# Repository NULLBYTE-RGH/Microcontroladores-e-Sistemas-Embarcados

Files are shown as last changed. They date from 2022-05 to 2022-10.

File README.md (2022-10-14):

Microcontroladores-e-Sistemas-Embarcados

# Projeto Fechadura Smart:

## Microcontrolador: raspberry pi pico

## Lista de componentes:

- Leitor de Digital DY50
- Teclado Matricial 4x4
- Solenoid 12v 0,9 A
- Display OLed SPI 128 X 32
- RFID MFRC-522
- Acelerometro MPU 6050
- Buzzer
- ESP 8266

## Placa e componentes Basicos:

- Placa de fenolite 10 x 20 Cm 
- Transistor TIP-310
- Reguladores [LM1117, L7805] 12 v -> 6 v e 6 v -> 3.3
- Resistores [300 Ω, 2.2k Ω] 300 Ω controle base do Transistor e 2.2k Ω PULL-UP na entrada RX do leitor de Digital
- 3 Capacitores 100 µF para remoção de ruído das entradas e saidas dos reguladores

## FrontEnd:

- React
- Bootstrap
- Fontawesome

- [x] O Servidor de aplicação sera um Raspberry Pi 3, o qual ira se comunicar com a fechadura por meio de WIFI com um AP gerado pelo ESP-8266 que ficara junto com a fechadura.
- [x] A comunicação se dara por meio de uma API REST.

### Trilhas

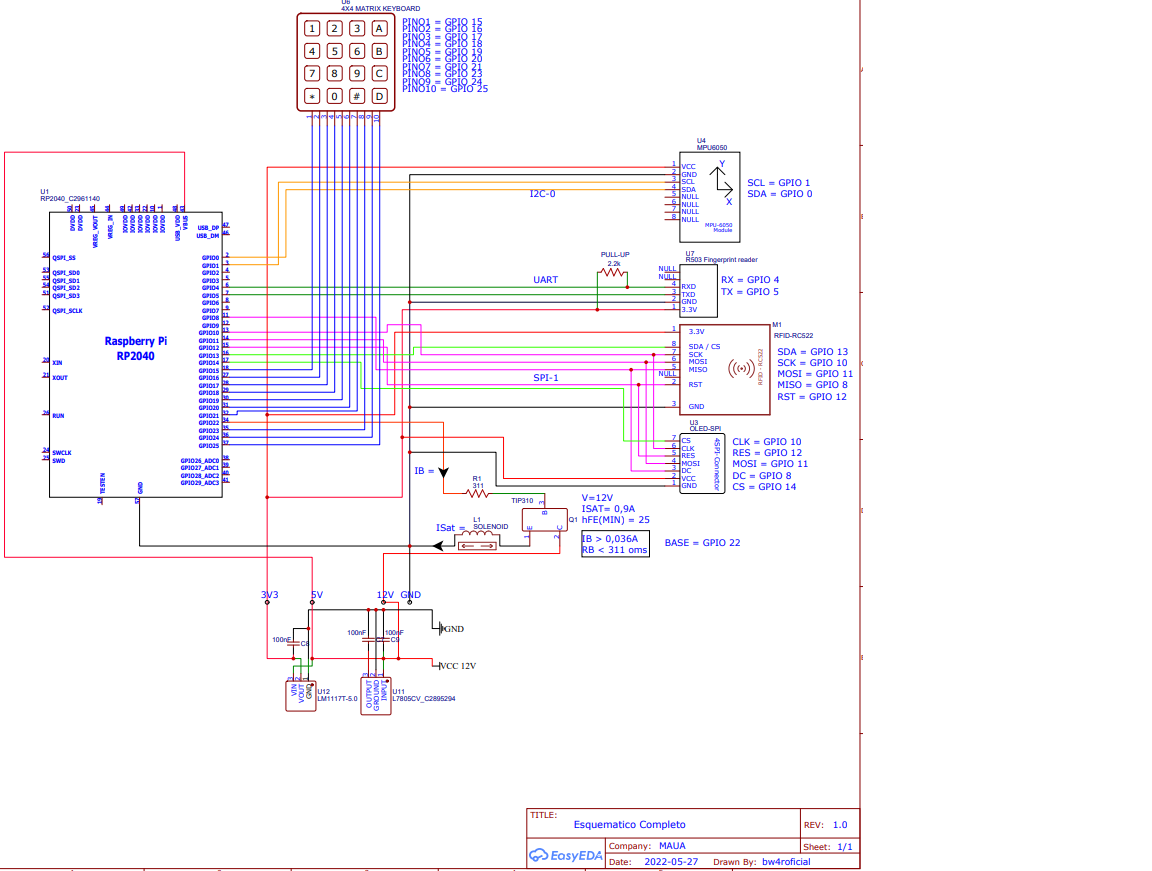
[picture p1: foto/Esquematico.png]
EsquemaDeTrilhas


### UI

FrontEnd

## BackEnd:

* Possui um barramento de MicroServiços com 2 serviços
* Os MicroServiços tem proposito de facilitar o gerenciamento das informaçoes, para não sobrecarregar os MicroControladores que ja gerenciam:
###### [X] Leitor de Digital
###### [X] RFID 
###### [X] Teclado numerico
###### [X] Giroscopio com acelerometro, para detectar arrombamento
###### [X] Visor Oled
###### [X] comunicação serial com o outro Microcontrolador ESP32 via UART
###### [X] abertura e fechamento do solenoid
###### [X} WIFI

* O Front faz atualizaçoes constantes sobre o estado da fechadura por meio de chamadas de conexao com o barramento a cada 1 segundo. Recebendo numero de usuarios cadastrados,nomes e tipos de autenticações. Juntamente com o nome do ultimo usuario a desbloquear a fechadura.

* O desbloqueio somente pode ser feito mediante previa autenticação 

* O cadastro de usuarios deve ser feito manualmente no banco de dados local volatil ou no arquivo dentro do Microcontrolador RaspPico.

* O acesso as funcionalidades que podem ser feitas devem ser acessadas via barramento, pelas seguintes partes:

[X] http://127.0.0.1:5000/GET -> para recebimento dos usuarios com senhas e ids (não deve ser utilizado pelo front por questao de segurança dos dados, é apenas para uso interno e autenticação entre os MiroSrviços)

+ ***A variavel Usuarios, dentro de Cadastro.js, sera obtida via requisição ao ESP32, atualmente esta sendo simulado via uma variavel com formatação incorreta de JSON***

* Ao se fazer a requisição para esse endereço via metodo *GET* é retornado a lista completa do banco de dados, isso inclui nomes, senhas etc.
* Com metodo *POST*, o Json retornado contem as mesmas partes que o riginal, porem, as senhas,IDs, e outras formas de autenticações sao substituidas por um * ('*')

[X] http://127.0.0.1:5000/ADD -> feito para cadastramento de usuarios novos ao banco de dados, o envio deve ser um Json, contendo (Nome,ID,SENHA,RFID,DIGITAL), no caso da fechadura real, tanto o RFID como a a Digital sao codigos templates, no RFID representa o codigo contido no cartao, e na Digital, representa o id da digital salva internamente no leitor.

[X] http://127.0.0.1:5000/DEST -> Utilizado para o destravamento da fechadura, deve ser utilizado mediante envio de um JSON, contendo o nome do usuario e uma das maneiras de autenticação, podendo ser Senha, RFID ou digital. Sera implementado o envio de um corpo de requisição contendo informaçoes para que o ESP32 coloque uma saida GPIO em nivel alto, ligado ao mesmo transistor que a RaspPico.

[X] http://127.0.0.1:5000/TRANC -> Utilizado para o travamento da fechadura, na fechadura real, isso nao cabe ao front, o controlador que gerencia o tempo de abertura, pois como a abertura é feita por meio de um solenoid, o mesmo consome muita corrente, e caso permaneça muito tempo aberto causara danos ao sistema. no caso da simulação o gerenciamento é feito no proprio front, esperando 3 segundos antes de mandar a requisição de fechamento.Na implementação real, o /TRANC tera apenas efeito ilustrativo, com o fechamento sendo feito via [Tranca.py](https://github.com/NULLBYTE-RGH/Microcontroladores-e-Sistemas-Embarcados/blob/dea4bf5e9c3107b0daa8275c070d7ebce901915b/Tranca.py)

[X] http://127.0.0.1:5000/ULT -> Feito para utilização interna entre os Serviçoes para alertar quem foi o ultimo a desbloquear a fechadura, por meio de um JSON contendo o nome da pessoa.

## Uso:
- Inicar o *Barramento* dentro da pasta MicroServiços/Barramento.js com o comando (node ./Barramento.js)
- Inicar o MicroServiço *Cadastro* dentro da pasta MicroServiços/Cadastro.js com o comando (node ./Cadastro.js)
- Inicar o MicroServiço *Fechadura* dentro da pasta MicroServiços/Fechadura.js com o comando (node ./Fechadura.js)
- Iniciar o servidor React dentro da pasta Raiz, com o comando (npm start)

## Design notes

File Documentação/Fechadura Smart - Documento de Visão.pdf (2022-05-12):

# Fechadura Smart Visão (Projeto Pequeno)

## Versão 1.0

Fechadura Smart | Versão: 1.0
Documento de Visão | Data: 20/03/2022
Confidencial | Página 2

# Histórico da Revisão

Data | Versão | Descrição | Autor
20/03/2022 | 1.0 | Criação do documento | João vitor sarti
20/03/2022 | 1.0 | Revisão geral | Mateus Rossini e Marcel Marques

# Índice Analítico

1. | Introdução | 4
1.1 | Referências | 4
2. | Posicionamento | 4
2.1 | Descrição do Problema | 4
2.2 | Sentença de Posição do Produto | 4
3. | Descrições dos Envolvidos e Usuários | 5
3.1 | Resumo dos Envolvidos | 5
3.2 | Resumo dos Usuários | 5
3.3 | Ambiente do Usuário | 5
4. | Visão Geral do Produto | 5
4.1 | Perspectiva do Produto | 6
5. | Outros Requisitos do Produto | 6

# Documento de Visão

### 1. Introdução

Este documento mostra uma visão geral sobre o produto: Fechadura Smart.

### 1.1 Referências

Não se aplica

### 2. Posicionamento

### 2.1 Descrição do Problema

O problema | As fechaduras convencionais possuem grandes problemas de segurança. Visto que, pessoas com conhecimento podem destravar praticamente qualquer tipo de fechadura convencional, e sem deixar vestígios de sua abertura. Há casos de esquecimento do travamento da tranca oque faz com que a pessoa tenha que voltar ao local para verificar. Outro problema é o fato de ficar preso a chaves, que dependendo da tranca pode ser grande e pesada. Junto a isso, a perda das mesmas faz com que seja necessário contratar um profissional para destrancar ou mesmo gerar uma nova chave, oque é custoso em tempo e dinheiro.
Afeta | Todas as pessoas que se preocupam com a segurança do seu local de trabalho, casa etc. E também as pessoas que tentam burlar essa segurança.
cujo impacto é | Uma maior segurança e confiabilidade.
uma boa solução seria | Uma fechadura digital, a qual teria diversos meios de autenticação, fazendo com que, mesmo perdendo uma das chaves digitais, seria possível acessar e desbloquear a fechadura. Com acesso constante com a internet ela pode notificar a situação atual dela e se houve tentativa de intrusão.

### 2.2 Sentença de Posição do Produto

Para | Todas a pessoas que querem um fator de segurança adicional além da tranca convencional.
O (nome do produto) | Fechadura Smart, conjuntura de Hardware e Software.
Que | Faz com que o travamento destravamento de portas e portões seja algo simples, seguro e confiável.
Diferente | De fechaduras mecânicas convencionais.
Nosso Produto | É indicado para qualquer pessoa que se sinta desconfortável em confiar em uma fechadura comum, a qual caso perca a chave, não terá mais acesso ao que está sendo guardado, e não possui nenhum sistema de alerta ou notificação caso esteja sendo violada, sendo só percebida a invasão quando o dono voltar ao local, muitas vezes não podendo fazer nada.

Descrições dos Envolvidos e Usuários

### 2.3 Resumo dos Envolvidos

Nome | Descrição | Responsabilidades
João Vitor, Mateus, Marcel | Equipe de Desenvolvimento | Responsável por todo desenvolvimento e aplicação do sistema.
João vitor | Gestor do projeto | Monitora e acompanha o desenvolvimento do projeto.
Marcel | Testador | Responsável por verificar se os dispositivos de segurança estão funcionando de acordo com o proposto.
João vitor, Mateus | Desenvolvimento do Hardware | Responsável por projetar e implementar os diferentes componentes elétricos e mecânicos.
João vitor, Mateus | Desenvolvimento da UI WEB | Responsável, por desenvolver e implementar uma interface gráfica para monitoramento gestão da fechadura

### 2.4 Resumo dos Usuários

Nome | Descrição
Pessoa “comum“ interessada em mais segurança. | Principal usuário do sistema - Responsável por cadastrar e administrar as pessoas autorizadas a utilizar a fechadura.
Terceiros | Usuário do sistema - Irão fazer uso ou não da fechadura, dependendo do controle de usuários feito pelo proprietário.

### 2.5 Ambiente do Usuário

A pessoa interessada em mais segurança possui diversos ambientes os quais deseja mais segurança, sejam eles internos. Possuem Telefones celulares que fazem uso de sistema (Android) e possuem um ou mais pontos de WIFI que tem alcance suficiente para cobrir todo o perímetro o qual se deseja ter mais segurança por um período 24/7. Os roteadores sem fio possuem capacidade de segurança WPA2 e de criar DMZs.

### 3. Visão Geral do Produto

A Fechadura Smart tem por objetivo dar uma maior tranquilidade para usuários que não se sentem confortáveis com as fechaduras padrões. Para isso a Fechadura Smart faz uso de 3 dispositivos de autenticação, os quais podem ser configurados para serem utilizados separadamente, ou em conjunto, visando autenticar o usuário, são eles:

- Reconhecimento Biométrico
- Senha Numérica
- Cartão RFID

O cadastro de senhas numéricas pode ser feito presencialmente ou remotamente via Celular. Já o cadastro biométrico e de cartão RFID deve ser feito na própria Fechadura. Mas após o cadastro as informações ficarão salvas na Nuvem.

Funções para o Dono da fechadura:

- Cadastro de usuários.
- Ser notificado em caso de tentativa de arrombamento.
- Excluir usuários.
- Ver estado da fechadura.
- Se notificado toda vez que a fechadura é aberta e fechada, e por quem foi feita a cação.
- Gerar senha de uso único ou temporária.

Funções para usuários da fechadura:

- Desbloqueio
- Receber notificações da fechadura, caso seja autorizado pelo dono.

Os dispositivos de Segurança são 2:

- Alerta sonoro
- Detecção de arrombamento por meio de giroscópio.

### 3.1 Perspectiva do Produto

A Fechadura Smart visa facilitar o acesso a portas e portões por pessoas conhecidas e dificultar o de indesejadas. Fazendo com que se tenha um monitoramento constante da situação da tranca.

### 4. Outros Requisitos do Produto

A interface deve ser WEB, compatível com Firefox.

A interface deve ser responsiva e do fácil acesso.

O sistema deve ser implementado em C e microPython na parte de Hardware e a parte WEB deve ser feita em NodeJs e Typescript

O sistema comporta apenas 1 Super Usuário, e até 10 usuários realizando consultas sobre estado da fechadura simultaneamente (se permitido pelo Super Usuário).

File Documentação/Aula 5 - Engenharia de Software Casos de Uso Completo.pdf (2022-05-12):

# Fechadura Smart Relatório Sintético de Modelo de Caso de Uso

## Versão 1

Fechadura Smart | Versão: <1.0>
Relatório Sintético de Modelo de Caso de Uso | Data: <18/04/2022>

# Histórico da Revisão

Data | Versão | Descrição | Autor
18/04/2022 | 1.0 | Listar Autorizados, Criar Usuário, Autenticar Usuário, Destrancar Porta | João Vitor Sarti
24/04/22 | 1.0 | Manter usuario, Listar acesso, Revogar acesso | Matheus Rossini
24/04/22 | 1.0 | Autenticar, Bloquear, Alertar intrusões | Marcel Marques

# Índice Analítico

1. | Diagrama de Caso de Uso | 4
2. | Catálogo de Atores | 4
3. | Nome do Caso de Uso | Erro! Indicador não definido.
3.1 | Breve Descrição | 5
4. | Fluxo de Eventos | 5
4.1 | Fluxo Básico | 5
4.2 | Fluxos Alternativos | 5
4.2.1. < Primeiro Fluxo Alternativo > | 9
4.2.2. < Segundo Fluxo Alternativo > | 6
5. | Pré-condições | 5
6. | Pós-condições | 5
7. | Regras de Negócio | 5

### 1. Diagrama de Caso de Uso

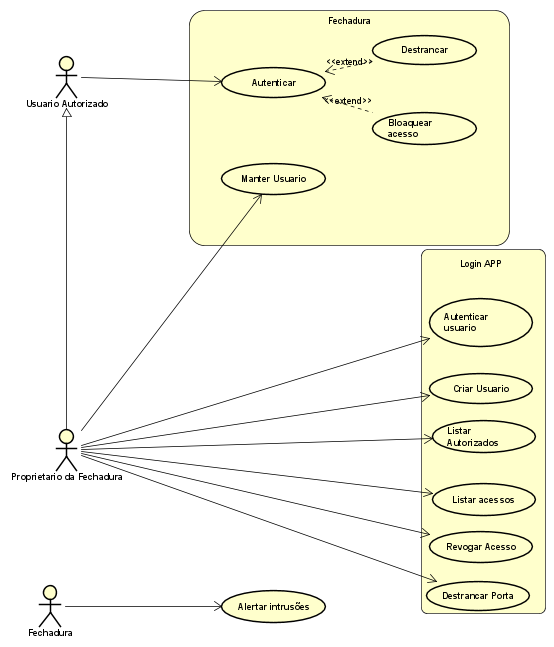
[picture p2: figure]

### 2. Catálogo de Atores

Nome | Descrição
Usuário Autorizado | Usuário que foi permitido a entrada, por meio do cadastro de senha numérica e ou digital e RfID.
Proprietario da Fechadura | Usuario e dono da fechadura.
Fechadura | Mecanismo da fechadura e eletronica envolvida.

### 3. Casos de uso:

Listar Autorizados

Breve Descrição
É feita a listagem de usuários cadastrados na fechadura. Mostrando Identificador, nome e senha.

Fluxo de Eventos

Fluxo Básico [FB]
1-O Dono da fechadura seleciona a opção (Listar usuarios)
2-É retornado uma lista dos usuarios cadastrados.[RN1]

Fluxo Alternativo: Não possui usuários Cadastrados
1. É mostrada uma notificação dizendo que não há usuários cadastrados.
2. Retorna a tela Inicial.

### Pré-condições

O ator dono da fechadura deve estar logado no APP. (caso de uso Autenticar Usuário)

### Pós-condições

Não se aplica

### Regras de Negócio

[RN1] é exibido 3 colunas contendo (ID, NOME, SENHA)

Criar Usuário

Breve Descrição
O criar usuário é dar o nome a um usuário no app, pois ao criar o usuário na fechadura, pelo fato de só ter teclado numérico, não é possível escrever o nome, então é atribuído um ID ao usuário, ele será mostrado no APP, mas para facilitar o reconhecimento, pode se atribuir um nome ao ID.

Fluxo de Eventos

Fluxo Básico
1. Escolhe no menu a opção criar usuário.
2. Insere o ID do usuário exibido na fechadura após o cadastro.
3. Atribui um nome ao ID[RN2].

Fluxo Alternativo
2- Ver ID pela função Listar Autorizados [RN3]

3- Escolhe no menu a opção criar usuário.

4-Insere o ID do usuário exibido Listar Usuários.

6- Atribui um nome ao ID[RN2].

Pré-condições
1. O ator dono da fechadura estar autenticado.
2. O usuário já deve ter sido cadastrado na fechadura.

Pós-condições
Não se aplica

Regras de Negócio
[RN2] após o cadastro de um usuário um ID será atribuído ao mesmo. Essa opção exibe um campo para inserção do ID, após o usuário, selecionar a opção de confirmação será exibido a ele uma tela para a digitação de um nome, podendo ter até 50 caracteres. Após inserir o usuário seleciona a opção de confirmação, o que fara com que um novo valor seja atribuído ao atributo nome no banco de dados.

[RN3] O ator dono da fechadura escolhe na opção e é exibido a ele uma tela com rolagem, na qual ele pode ver todos os usuários atualmente cadastrados na fechadura, tendo 2 campos, ID e nome. Caso o nome ainda não tenha sido atribuído, constara como NULL.

Autenticar Usuário

Breve Descrição
A autenticação é feita pelo servidor através do APP, para ter acessos aos recursos de gerenciamento da fechadura.

Fluxo de Eventos

Fluxo Básico [FB]
1. dono da Fechadura inicia o aplicativo no SmartPhone.
2. O ator dono da fechadura se autentica no APP [RN1].

Fluxo Alternativo [FA]
O ator dono da fechadura cria uma conta no APP [RN2].

Pré-condições
O usuário já deve ter sido cadastrado na fechadura. [FB]

Pós-condições
O usuário Digitado é validado no banco de dados, e ele será utilizado em qualquer operação na fechadura. [FB]

[FA] O cadastro é salvo no banco de dados e o usuário retorna a tela inicial do APP, o qual pede o Login. [FB]

Regras de Negócio
[RN1] é exibido para o ator dono da fechadura as opções:

Entrar

Criar conta

A opção (Entrar) pede que o ator Dono da fechadura digite seu e-mail e senha já cadastrados. Então a tela com as opções é exibida.

[RN2] (criar usuário), será exibida uma tela que pede que ele insira um E-mail e um senha de no mínimo 8 caracteres, sendo assim seu cadastro será efetuado e ele poderá acessar as funcionalidades do APP, sendo a primeira necessária, a (Cadastrar fechadura), a qual pede que seja inserido o número mostrado pela fechadura após energizada. Assim sendo vinculada o ID da fechadura com a conta do Dono.

Destrancar

Breve Descrição
A opção de destrancar a porta ocorre dentro do app da fechadura, não exigindo contato com a fechadura. Sendo feito somente pelo dono da fechadura.

Fluxo de Eventos

Fluxo Básico
1. O ator dono da fechadura se autentica no APP [RN1].
2. Escolhe no menu a opção (Destrancar).
3. A fechadura é destrancada.

Fluxo Alternativo
Não se aplica

Pré-condições
O Ator dono da fechadura já deve estar cadastrado e a fechadura também, e ambos com conexão com a internet.

Pós-condições
A fechadura se destranca.

Regras de Negócio
[RN1] é exibido para o ator dono da fechadura as opções:

Entrar

Criar conta

A opção (Entrar) pede que o ator Dono da fechadura digite seu e-mail e senha já cadastrados. Então a tela com as opções é exibida.

Caso escolha (criar usuário), será exibida uma tela que pede que ele insira um E-mail e um senha de no mínimo 8 caracteres, sendo assim seu cadastro será efetuado e ele poderá acessar as funcionalidades do APP, sendo a primeira necessária, a (Cadastrar fechadura), a qual pede que seja inserido o número mostrado pela fechadura após energizada. Assim sendo vinculada o ID da fechadura com a conta do Dono.

Manter Usuário

Breve Descrição
Tem como objetivo criar e excluir informações dos usuários locadas no banco de dados.

Fluxo de Eventos

Fluxo Básico
1. sistema exibe o menu de opções com as opções Cadastrar [FA1] e Excluir [FA2] .
2. ator Proprietário da Fechadura solicita a opção que deseja realizar.

Fluxos Alternativos

4.2.1. Fluxo Alternativo 1: Cadastrar usuário.
1. O sistema solicita que insira uma senha numérica.
2. O ator Proprietário da Fechadura insere a informação e confirma [RN1].
3. O sistema devolve um ID para o usuário.
4. O sistema salva os dados no banco de dados.
4.2.2. Fluxo Alternativo 2: Excluir Usuário.
1. O sistema solicita que insira o ID de um usuário.
2. O ator Proprietário da Fechadura insere a informação e confirma.
3. O sistema exclui o usuário do banco de dados.

4.2.3 Fluxo Alternativo 3: Usuário Inexistente (Excluir Usuário)

1. O sistema solicita que insira o ID de um usuário.
2. O ator Proprietário da Fechadura insere a informação e confirma.
3. O sistema alerta que o ID inserido não existe no banco de dados.
4. Sistema pede novamente que seja informado um ID.

### Pré-condições

O usuário autenticado deve ser o Proprietário da Fechadura.

### Pós-condições

Não se aplica.

### Regras de Negócio

[RN1] Senha numérica deve conter exatamente 6 dígitos.

Listar Acessos

Breve Descrição
Listar acessos permite que seja exibido os usuários aos quais tentaram se autenticar.

Fluxo de Eventos

Fluxo Básico
1. O ator proprietário da fechadura realiza uma autenticação no app.
2. O Sistema verifica e permite o acesso.
3. O Sistema exibe um menu de opções.
4. Ator proprietário solicita “Listar Acessos” em determinado período.
5. Sistema verifica o banco de dados e retorna os acessos no período solicitado. Os dados apresentados são: nome, data, hora, status (Aprovado ou Negado).

Fluxos Alternativos

4.2.1. Fluxo alternativo 1: A Listagem não retornou resultados
1. Sistema informa que a busca não retornou resultados.
2. Fluxo retorna ao passo 3 do fluxo básico.

### Pré-condições

É necessário que o ator “Proprietário da Fechadura” tenha sido autenticado pelo fluxo “Autenticar Usuário”.

### Pós-condições

Não se aplica.

### Regras de Negócio

Não se aplica.

Revogar Acesso

Breve Descrição
Permite que o proprietário da fechadura remova acesso de determinado usuário.

Fluxo de Eventos

Fluxo Básico
1. O ator proprietário da fechadura realiza uma autenticação no app.
2. O Sistema verifica e permite o acesso.
3. O Sistema exibe um menu de opções.
4. Ator proprietário solicita “Revogar Acesso”.
5. O Sistema exibe todos os usuários cadastrados.
6. Ator Proprietário seleciona o usuário que deseja revogar o acesso.
7. Sistema exclui permanentemente o usuário com acesso revogado.

Fluxos Alternativos

4.2.1. Fluxo alternativo 1: Usuário revogado é o proprietário da fechadura.
1. Sistema informa que este usuario não pode ser excluído.
2. Fluxo retorna ao passo 5 do fluxo básico.
4.2.2. Fluxo alternativo 2: Revogar acesso solicitado por Usuário Autenticado.
1. Sistema informa que este usuario não tem acesso a função Revogar Acesso.
2. Fluxo retorna ao passo 3 do fluxo básico.

### Pré-condições

É necessário que o ator “Proprietário da Fechadura” tenha sido autenticado pelo fluxo “Autenticar Usuário”.

### Pós-condições

Usuário revogado perde acesso imediato a fechadura, remoção total do banco de dados.

### Regras de Negócio

Não se aplica.

Autenticar

### Breve Descrição

É realizado a checagem para autenticação do usuário tentando abrir a fechadura.

### Fluxo de Eventos

### Fluxo Básico

1.O usuário põe o dedo no leitor
2. A leitura da digital é enviada para o Sistema de cadastros que retorna os dados da digital: Código, Nome do usuário, e RG. [FA1], [FA2]

3.A fechadura se abre[RN1].

### Fluxos Alternativos

[FA1] Fluxo Alternativo 1: Digital não Identificada

1.O sistema não conseguiu verificar a digital.

2.O sistema pede ao usuário para colocar novamente o dedo no leitor[RN2].

4.A leitura da digital é enviada para o Sistema de cadastros que retorna os dados da digital: Código, Nome do usuário, e RG.

5.A fechadura se abre[RN1]

[FA2] Fluxo Alternativo 2: Digital não cadastrada
1.O sistema não conseguiu verificar a digital

2.O sistema pede ao usuário para colocar novamente o dedo no leitor[RN2]

3.A leitura da digital é enviada para o Sistema de cadastros que retorna digital não cadastrada.

4.A fechadura não se abre [RN3].

### Pré-condições

Sistema espera uma nova leitura de digital.

### Pós-condições

1.Sistema espera uma nova leitura de digital.

2.Sistema está travado por muitas tentativas falhas de uso.[RN3]

### Regras de Negócio

[RN1] Se a digital for válida a fechadura se abre.

[RN2] Se a digital não for válida, sistema pede para colocar o dedo novamente.

[RN3] Se após 4 tentativas a digital for inválida, a fechadura trava por 20 minutos.

Bloquear Acesso

Breve Descrição
Sistema bloqueia o acesso à fechadura eletrônica.

Fluxo de Eventos

Fluxo Básico
1.Usuário coloca a digital no leitor.

2.O sistema checa o banco de dados(cadastros).

3.O sistema não encontra digitais compatíveis

4.Repetindo o processo até 4 vezes, a fechadura é bloqueada.[RN2] 5.É enviado um alerta para o dono da fechadura.[RN1]

Fluxos Alternativos
[FA1] Fluxo Alternativo 1: Uso de força na fechadura

1.O sistema detecta anomalias na fechadura[RN3]

2.O sistema bloqueia o acesso a fechadura.
3.É enviado um alerta para o dono da fechadura.[RN1]

### Pré-condições

1.Sistema não encontra leitura de digital no banco de dados.

2.Sistema detecta por sensores uso de força na fechadura.

### Pós-condições

1.Sistema espera liberação do proprietário.

### Regras de Negócio

[RN1] Se a fechadura tiver acesso bloqueado, envia um alerta ao proprietário.

[RN2] Se após 4 tentativas a digital for inválida, a fechadura trava por 20 minutos.

[RN3]Sensores da fechadura detectam uso de força na mesma.

Alerta de Intrusões

Breve Descrição
Sistema aciona um alerta para o usuário principal.

Fluxo de Eventos

Fluxo Básico
1.Usuário coloca a digital no leitor.

2.O sistema checa o banco de dados(cadastros).

3.O sistema não encontra digitais compatíveis.

4.Repete passo 1,2 e 3 até 4 vezes.
5.É enviado um alerta para o dono da fechadura.[RN1]

Fluxos Alternativos
[FA1] Fluxo Alternativo 1: Uso de força na fechadura

1.O sistema detecta anomalias na fechadura[RN2]

2.O sistema bloqueia o acesso a fechadura.
3.É enviado um alerta para o dono da fechadura.[RN1]

### Pré-condições

Não se aplica.

### Pós-condições

Não se aplica.

### Regras de Negócio

[RN1] Se a fechadura tiver acesso bloqueado, envia um alerta ao proprietário. [RN2]Sensores da fechadura detectam uso de força na mesma.

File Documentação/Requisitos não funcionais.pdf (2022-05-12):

## Requisitos não funcionais: Fechadura Smart

Integrantes:

Joao vitor Sarti 18.01224-8

Marcel Marques Caceres 17.00648-0

Matheus Rossini de Souza 18.01060-0

Desempenho:

Identificador | RNF001 | Categoria | Desempenho
Nome | Tempo para reconhecimento de Digital e consumo de energia.
Data de criação | 27/04/22 | Autor | João Vitor Quirino Sarti
Versão | 1 | Prioridade | Essencial

## Descrição

O reconhecimento da digital deve ser feito inteiramente pelo modulo de reconhecimento. Possuir processamento integrado da impressão digital o qual se encarrega da parte de processamento ótico e também possui memoria integrada para realizar o armazenamento das minucias. O modulo tem que possuir baixo consumo de energia e interface simples, junto a alta confiabilidade, velocidade de reconhecimento, boa adaptabilidade aos dedos secos e molhados e busca rápida de impressões digitais.

O firmware deve possuir função de autoaprendizagem, no processo de reconhecimento de impressão digital, depois de extrair novos valores da característica de impressão digital, os valores da característica são fundidos nas características anteriores da impressão digital, para cada vez o reconhecimento ficar mais preciso e ágil.

A comunicação com o microcontrolador deve ser feita via UART, dessa forma os dados podendo ser serializados, levando um número menor de vias e podendo ter sinal de clock separado do controlador.

A alimentação deve ser feita com 3V3, vinda de uma fonte externa a do microcontrolador, visto que o consumo de corrente elevado (140 mA) junto aos outros módulos não seria suportado pelo P65M15.

O sistema deve ser capaz de armazenar até 200 digitais com nível de aceitação falsa <0.001%, sendo assim cada arquivo de assinatura deve possuir, 256 bytes e os de modelo 512 bytes, totalizando uma memória de 150 Kb.

O tempo de busca e confirmação deve ser <2.0 segundos sendo assim a comunicação UART deve ter no mínimo uma taxa de 9600 b/s podendo chegar até 57600 b/s

Identificador | RNF001 | Categoria | Desempenho
Nome | Tempo para reconhecimento do Token RFID e consumo de energia.
Data de criação | 27/04/22 | Autor | João Vitor Quirino Sarti
Versão | 1 | Prioridade | Essencial

Descrição

O leitor RFID deve atuar na frequência de 13.56mhz e ter um consumo de 3v3 volts para a aplicação. Deve ter uma interface de comunicação simples e que possibilite o uso da mesma via para múltiplos dispositivos, como comunicação I2C ou SPI. A corrente não pode ultrapassar (26 mA) durante operação e quando estiver ocioso deve ter um consumo de 10 mA a 1 Ma.
O armazenamento das credenciais deve ser feito em um arquivo interno ao microcontrolador sendo 96 bits por usuário (sendo comportados 200 usuários) sendo 8 bits reservados a identificação e 88 bits de informações do usuário, totalizando um armazenamento total de 2,3 Kb.
O tempo entre transmissão de sinal, e confirmação da identidade deve levar no máximo 1 segundo.

Identificador | RNF003 | Categoria | Segurança
Nome | Criptografia e armazenamento seguro
Data de criação | 27/04/22 | Autor | Marcel Marques
Versão | 1 | Prioridade | Essencial

Descrição

O sistema aceitará senhas de no mínimo 6 dígitos, sendo salva como um HASH MD4 de 16 bytes, sem ser texto puro ou criptografada.

A cada novo acesso, a autenticação deverá ser realizada novamente, de maneira integral, e o acesso será seguro com autenticação em nível do servidor e em nível de aplicação.

O sistema poderá cadastrar até 200 usuários simultâneos

O alarme do sistema mandará um aviso ao telefone móvel do proprietário. Tipo. A cada novo acesso, a autenticação deverá ser realizada novamente, de maneira integral.

Deverá haver uma política de segurança que assegure que, a cada mês, a senha de cada um dos usuários citados expire e precise ser renovada, e que tenha critérios de complexidade alta de senhas (vide o documento da área de infraestrutura da empresa que tenha detalhes sobre os níveis de complexidade exigidos para cadastro de senhas); tudo isso deve ser considerado no tratamento de exceções no contexto deste requisito.

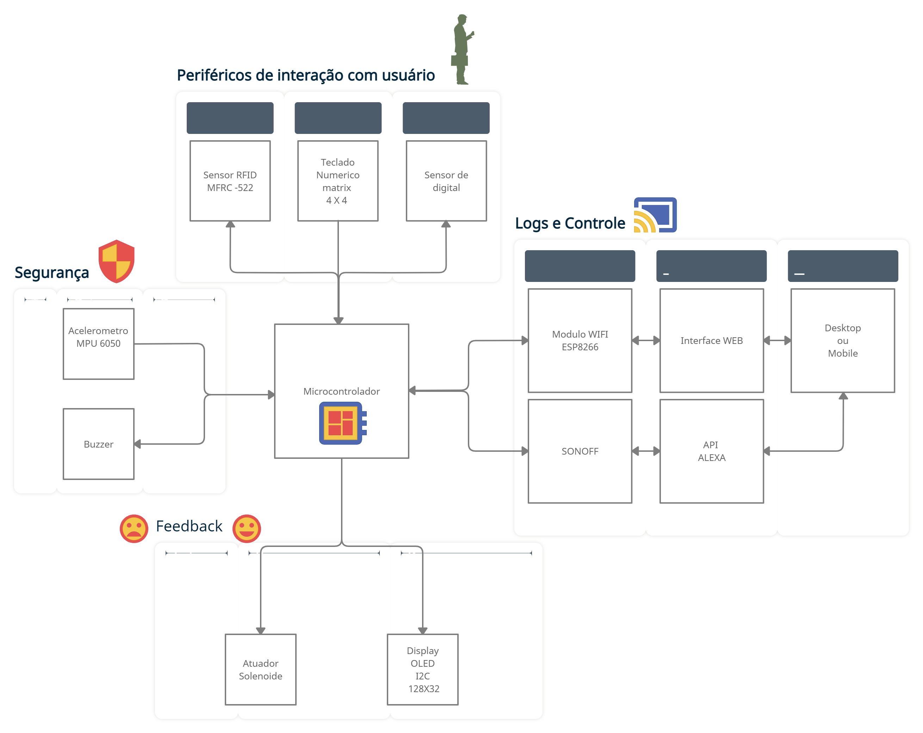
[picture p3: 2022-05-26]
Documentação/Diagrama de blocos sem UML.jpg

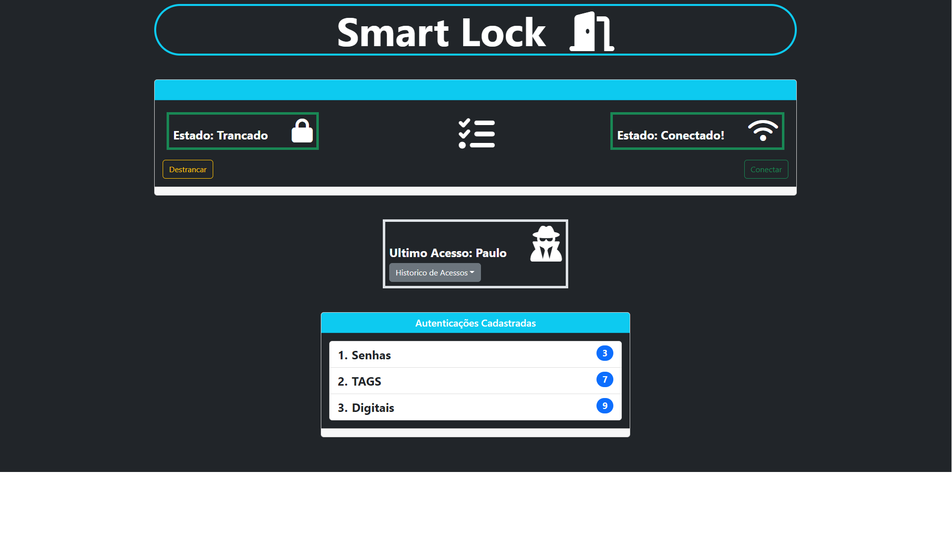
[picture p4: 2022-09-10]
foto/Site Fechadura.png

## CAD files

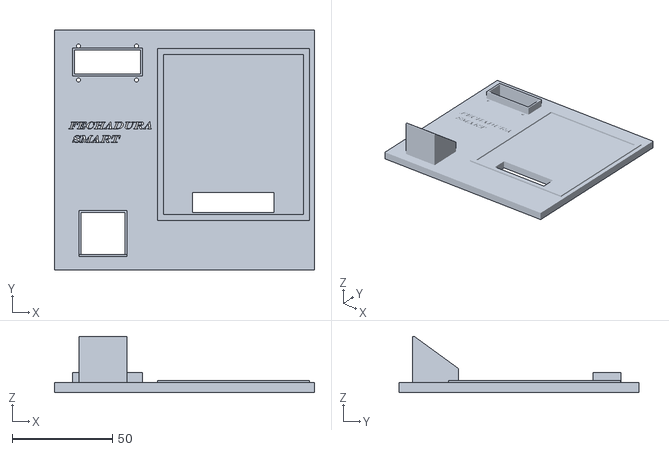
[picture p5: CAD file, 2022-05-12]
Modelos 3d/JoaoVitor_Frente Nova_3D_1.STL
130.0 x 120.0 x 28.0

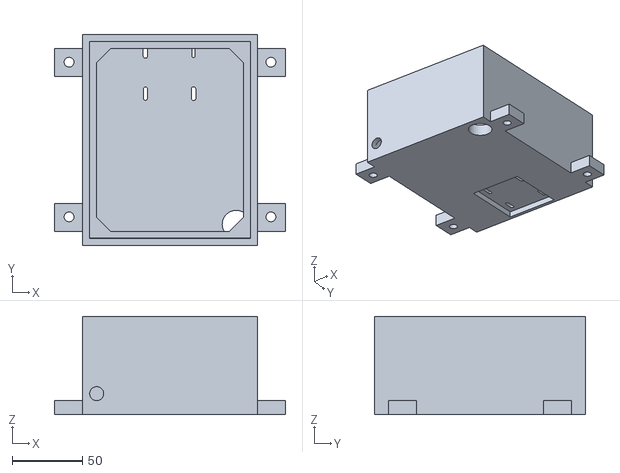
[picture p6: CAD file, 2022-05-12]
Modelos 3d/Joao_Vitor_Suporte solenoide_3D_1.STL
164.2 x 150.0 x 70.0

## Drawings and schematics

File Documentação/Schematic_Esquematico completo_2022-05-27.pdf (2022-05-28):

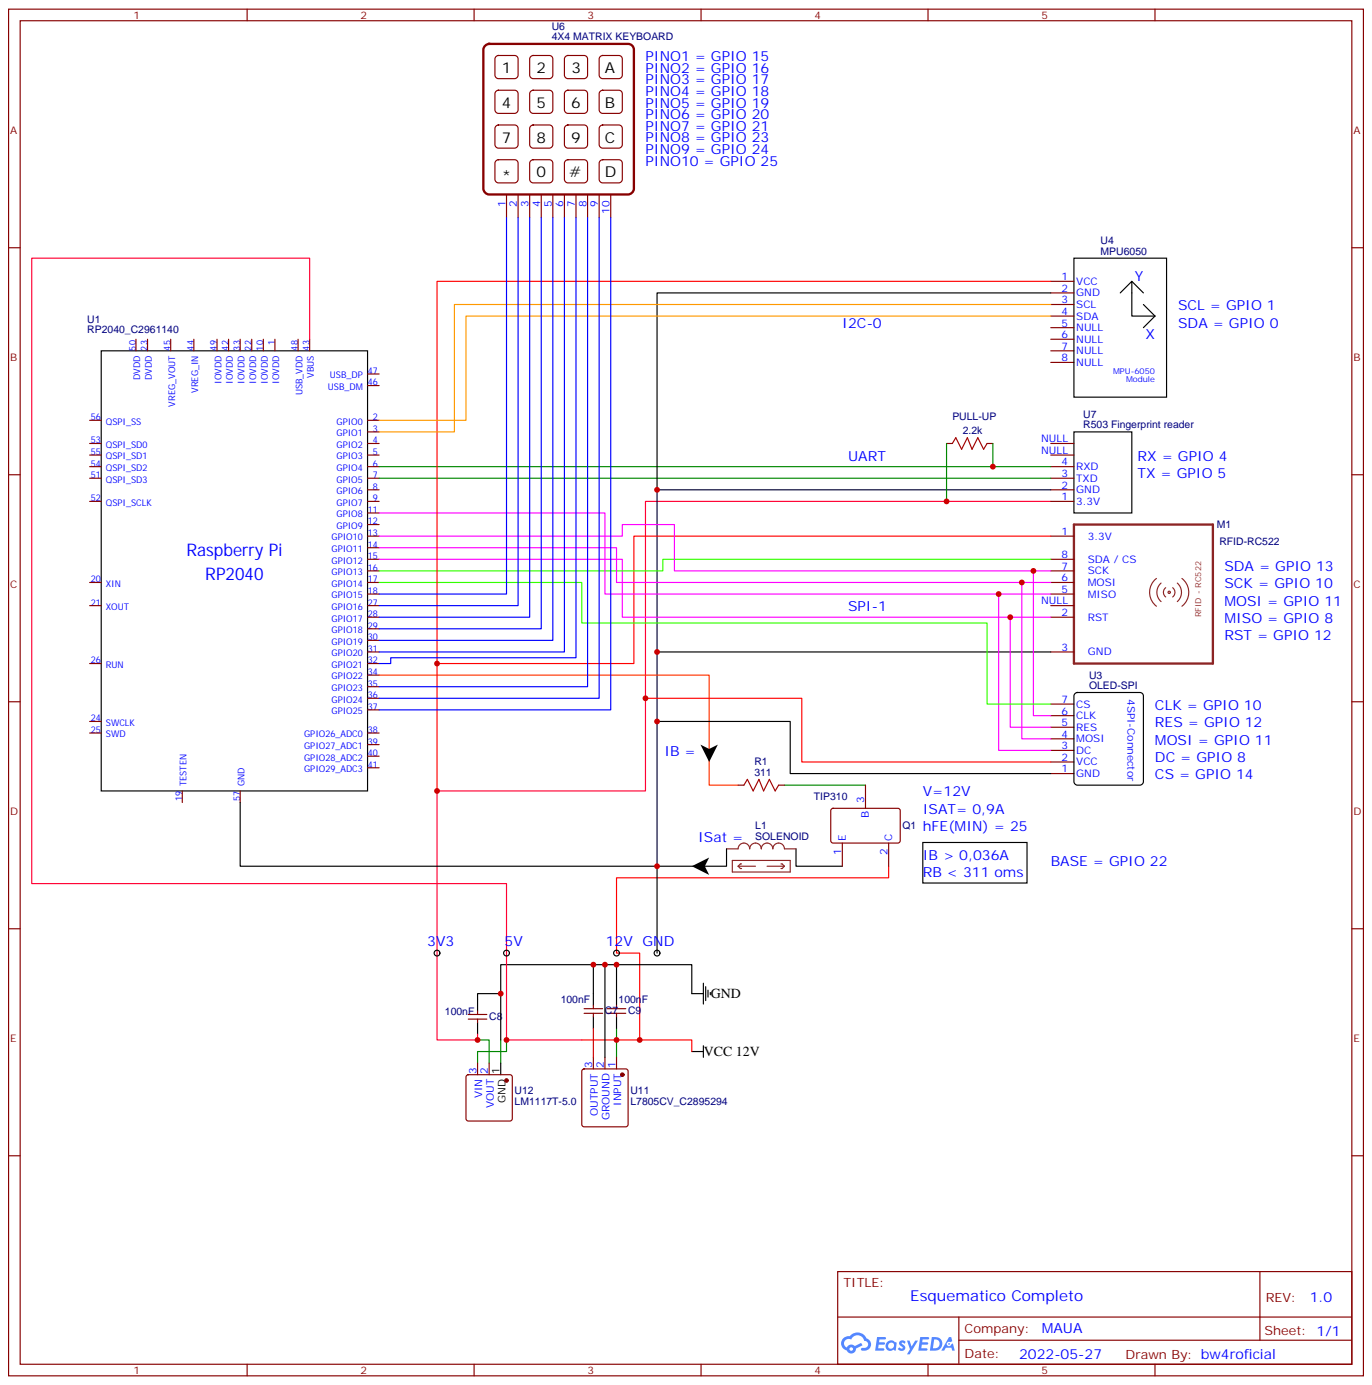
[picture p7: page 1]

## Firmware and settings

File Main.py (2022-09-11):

import leitorDigital
from machine import Pin
import Tranca
import time
import Teclado
import RFID
import Display
import Giroscopio

def IniciarDigital():
    try:
        leitor = leitorDigital.leitorDigital()
        return leitor
    except Exception as e:
        try:
            leitor = leitorDigital.leitorDigital()
            return leitor
        except Exception as e:
            print(e)
            
def IniciarSistema():
    teclado = Teclado.Teclado()
    rfid = RFID.RFID()
    digital = IniciarDigital()
    while True:
        print("Escolha uma Opção: A, B, C")
        opcao = teclado.LerTeclado(1)
        if (opcao == "A"):
            teclado.Validar_Senha()
        elif(opcao == "B"):
            rfid.Validar_Tag()
        elif(opcao == "C"):
            digital.ValidarDigital()
        
        

IniciarSistema()

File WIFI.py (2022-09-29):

try:
  import usocket as socket
except:
  import socket

import network

import esp
import UART_SYN_ACK
from machine import Pin
import json
esp.osdebug(None)

import gc
gc.collect()
serial = UART_SYN_ACK.UART_SYN()
ssid = 'MicroPython-AP'
password = '124679999'
Pino_SYN = Pin(23, Pin.OUT)

ap = network.WLAN(network.AP_IF)
ap.active(True)
ap.config(essid=ssid, authmode=network.AUTH_WPA_WPA2_PSK, password=password)

while ap.active() == False:
  pass

print('Configuracao Completa')
print(ap.ifconfig())

def web_page():
    try:
        Pino_SYN.value(1)
        resposta = serial.Serial(1)
        Pino_SYN.value(0)
        resposta = resposta[0]+'"'+resposta[1:len(resposta)-1]+'"'+resposta[-1]
        resposta = resposta.replace("'",'"')
        resposta = resposta.replace(",,",",")
        resposta = resposta.replace("::",":")
        resposta = resposta.replace("{{","{")
    except Exception as e:
        print(e)
        resposta = "ocorreu um Erro !"
        Pino_SYN.value(0)
    html = resposta
    return html

s = socket.socket(socket.AF_INET, socket.SOCK_STREAM)
s.settimeout(None)
s.bind(('', 80))
s.listen(5)

while True:
  conn, addr = s.accept()
  print('Recebendo Solicitacao de %s' % str(addr))
  request = conn.recv(1024)
  print('Requisicao = %s' % str(request))
  response = web_page()
  conn.send(response)
  Pino_SYN.value(0)
  conn.close()

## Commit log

2022-09-27 Update UART_SYN_ACK.py
    exemplo de saída:
    SYN enviado...
    Aguardando Confirmacao...
    ACK Recebido!
    Iniciando Comunicacao...
    Enviando tamanho do buffer...
    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
2022-09-27 Update UART_SYN_ACK.py
    Encapsulamento em Classe e aprimoramento de robustez
2022-09-29 Fragmentação
    Adicionado Fragmentação de Pacotes maiores que 20 Bytes
2022-09-29 Troca de Append para Concat
    Saida Antiga:
    ["[{'senha': '1111', '", "'rfid': '1485898912'", "', 'digital': '0', '", "'id': '1', 'nome': '", "'joao'}, {'senha': '", "'2222', 'rfid': '204", "42135750', 'digital'", "': '0', 'id': '2', '", "'nome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
2022-09-29 ESP no modo Ponto de acesso
    Ao receber um requisição, é colocado o pino 23 em HIGH para indicar ao RaspPico que deve se Iniciar a comunicação UART, feito isso o conteúdo fragmentado é restaurado em JSON e enviado ao cliente.
2022-09-29 Novo parâmetro e Correção de Bugs
    [UART_SYN_ACK.py]
2022-10-10 Removido botão de confirmação
    Estado atualizado a cada tecla pressionada.
